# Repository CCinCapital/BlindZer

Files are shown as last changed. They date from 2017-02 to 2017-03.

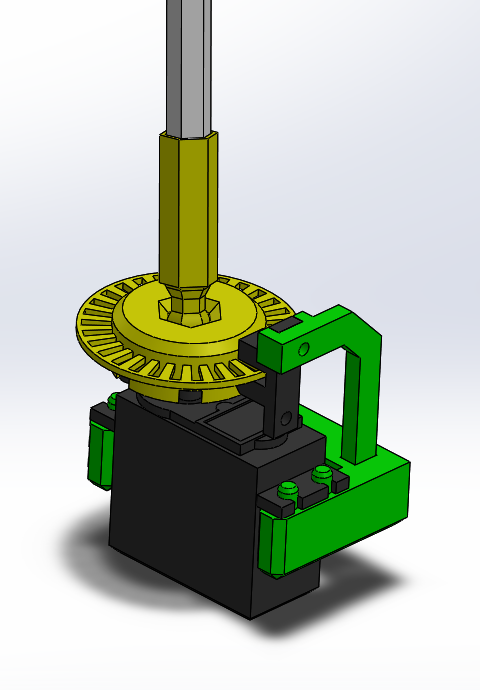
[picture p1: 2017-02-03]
Assembling Instruction/12. Fully Assembled (2).PNG

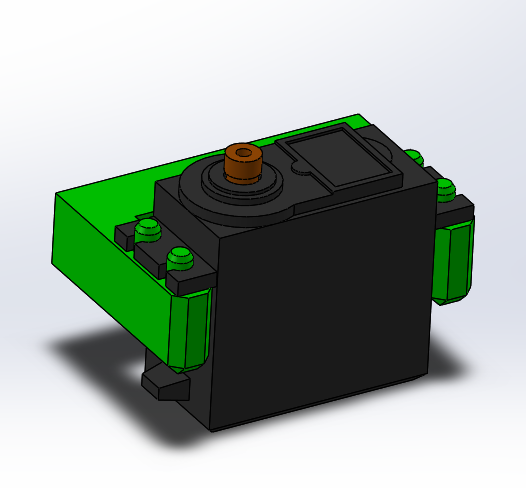
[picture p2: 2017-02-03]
Assembling Instruction/06. Servo Mount Assembly (2).PNG

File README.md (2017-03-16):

# BlindZer
Wireless enabled Window Blinds Roller<br>

<br>

### Video DEMO
[to be inserted HERE]
### Assembly Preview
<a href="https://github.com/CCinCapital/BlindZer/blob/master/3D%20STL%20Files/Assemly_PREVIEW.STL">Click Here</a>
### Compatibility
    + Window Blinds with hexagonal Rod. [Rod thickness: 8mm edge to edge]
### Software Requirement
    + Arduino IDE with ESP8266 Board Support package installed
    + Python
### Hardware Requirement
    + Access to 3D printer
    + Node MCU v0.9
    + TowerPro MG996R Servo Pack [Modified for continous rotation]
    + IRL2703 or any NMOS that able to drive Id > 500ma when Vgs = 3.3v
    + TCST2103 Optical Interrupter
    + Few Resistors [2K x1 ; 2.2K x2; 3.3K x1; ]
    + Breadboard or Protoboard
    + Jumper wires
    + Scerw [M3 x1 ; Wall Mounting x2 ]
    + Soldering Station & Solder & Flux
    + Phillip screwdriver 
    + Wire cutter & Pilers
### Installation
#### Hardware
       ----- Circuit -----
    1. Build the circuit by refering ../Schematic/BlindZer_Sche.pdf
    
       ----- Part Assembly -----
    1. Navigate to "../3D STL Files/" folder of this project
    2. 3D print all the .STL part at 1:1 ratio [mm]
    3. Assemble the 3D printed part refer to the instruction in "../Assembling Instruction/"
    
       ----- Modify the Servo -----
    1. Modify the servo for continous rotation [Follow the instruction below]
<a href="http://www.instructables.com/id/How-to-hack-a-servo-for-continuous-rotation-Towe/?ALLSTEPS">Click here to learn "How to modify a servo for continous rotation?"</a>
#### Software
    1. Clone or Download this repository
    2. Install the runtime environment
    
       ----- Modify Arduino Code -----
    3. Navigate to the Code at ../Code/Main/Main.ino
    4. Modify the code (Change the SSID and PASSWORD parameter) 
    5. Upload code to your board and observe the Serial Terminal to find line "Use this URL to connect: http://xxx.xxx.xxx.xxx"
    6. Record the URL
  
       ----- Modify Python Code -----
    7. Navigate to the Script at ../Code/GUIhttpRequest.py   
    8. Edit the Code and change the [self.IP = "xxx.xxx.xxx.xxx"] parameter to the IP recorded (URL without 'http://')

## Usage
       ----- Powering the BlindZer -----
    1. Use USB cable (directly plug into the onboard usb jack of NodeMCU)
    2. Powering using 4 x AA battery through the 2Pin header (see schematic)

       ----- Control using Webpage -----    
    1. Open the URL in a WebBrwoser
    
       ----- Control using Python GUI -----
    1. Run the GUIhttpRequest.py
## TODO
       ----- Firmware -----
    - Remember current position
    - implement Sleep(); and Weakup();
    
       ----- Python -----
    - Automatically control the BlindZer based on weather/time/Sun Height information
## Contributing
    + Fork it
## Credits
    http://www.instructables.com/id/Quick-Start-to-Nodemcu-ESP8266-on-Arduino-IDE/  by Magesh Jayakumar
## License
<br />This work is licensed under a <a rel="license" href="http://creativecommons.org/licenses/by-nc-sa/4.0/">Creative Commons Attribution-NonCommercial-ShareAlike 4.0 International License</a>.

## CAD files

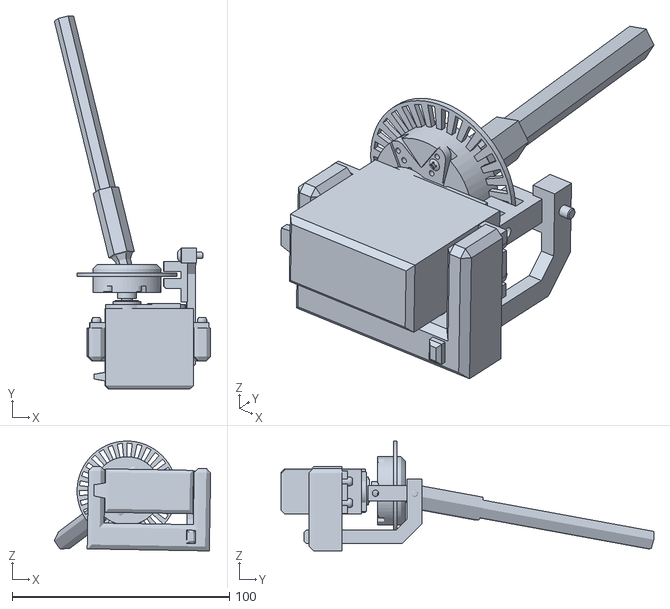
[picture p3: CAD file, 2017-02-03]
3D STL Files/Assemly_PREVIEW.STL
72.1 x 171.9 x 50.6

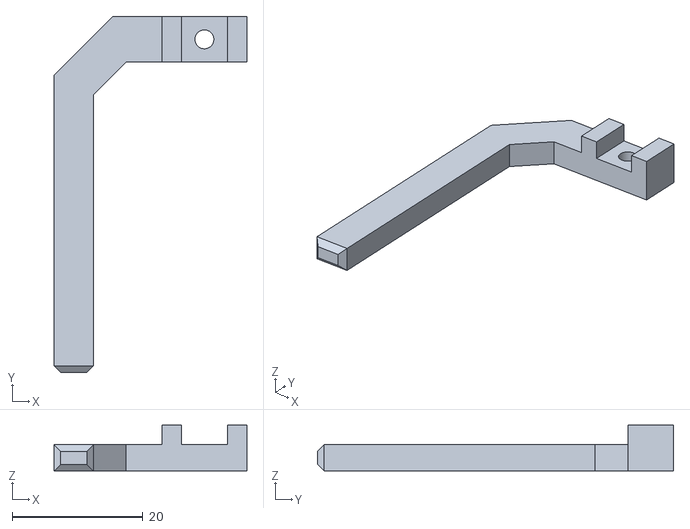
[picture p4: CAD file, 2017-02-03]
3D STL Files/InterrupterMount.STL
29.5 x 54.5 x 7.00

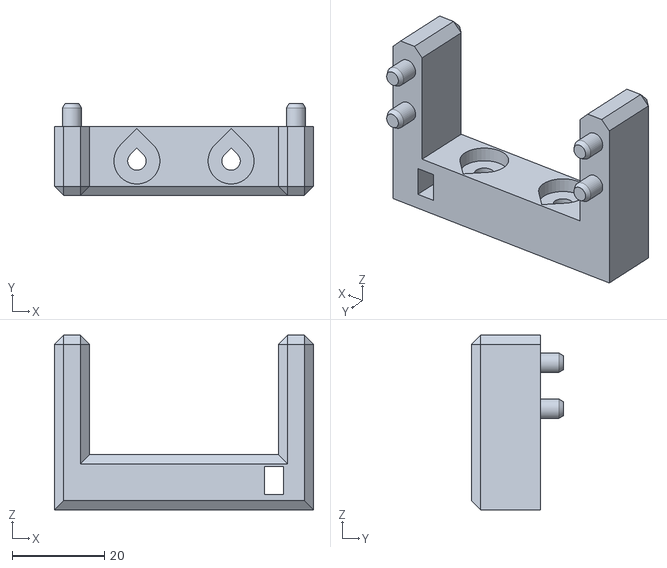
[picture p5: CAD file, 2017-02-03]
3D STL Files/ServoMount.STL
56.3 x 20.0 x 38.0

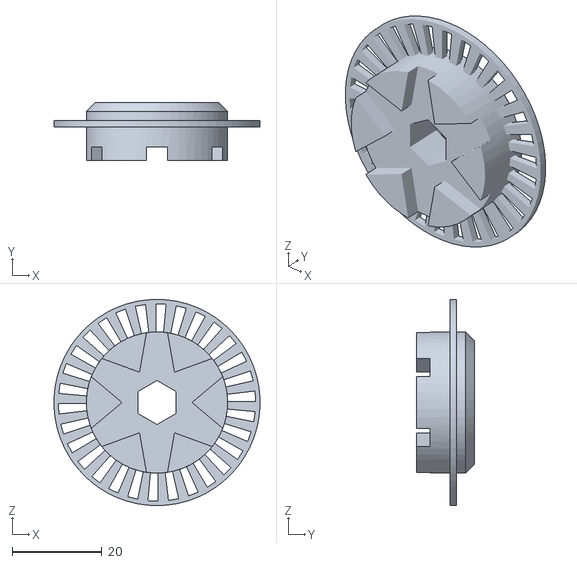
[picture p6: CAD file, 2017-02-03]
3D STL Files/ServolClampWithEncoder.STL
45.9 x 13.0 x 46.0

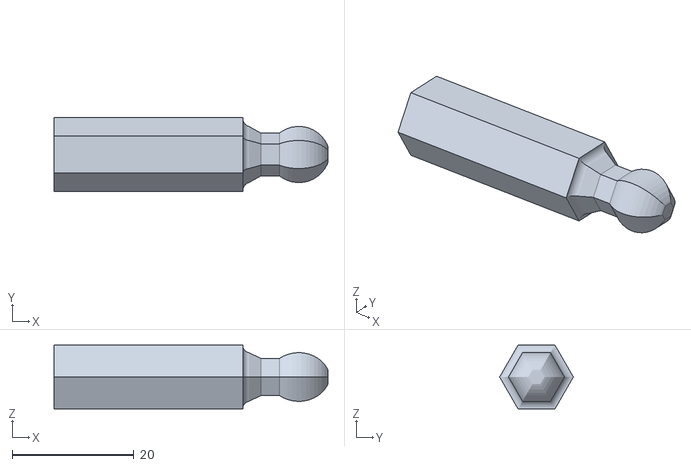
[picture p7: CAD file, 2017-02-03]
3D STL Files/BlindsRodAdapter.STL
45.0 x 12.1 x 10.5

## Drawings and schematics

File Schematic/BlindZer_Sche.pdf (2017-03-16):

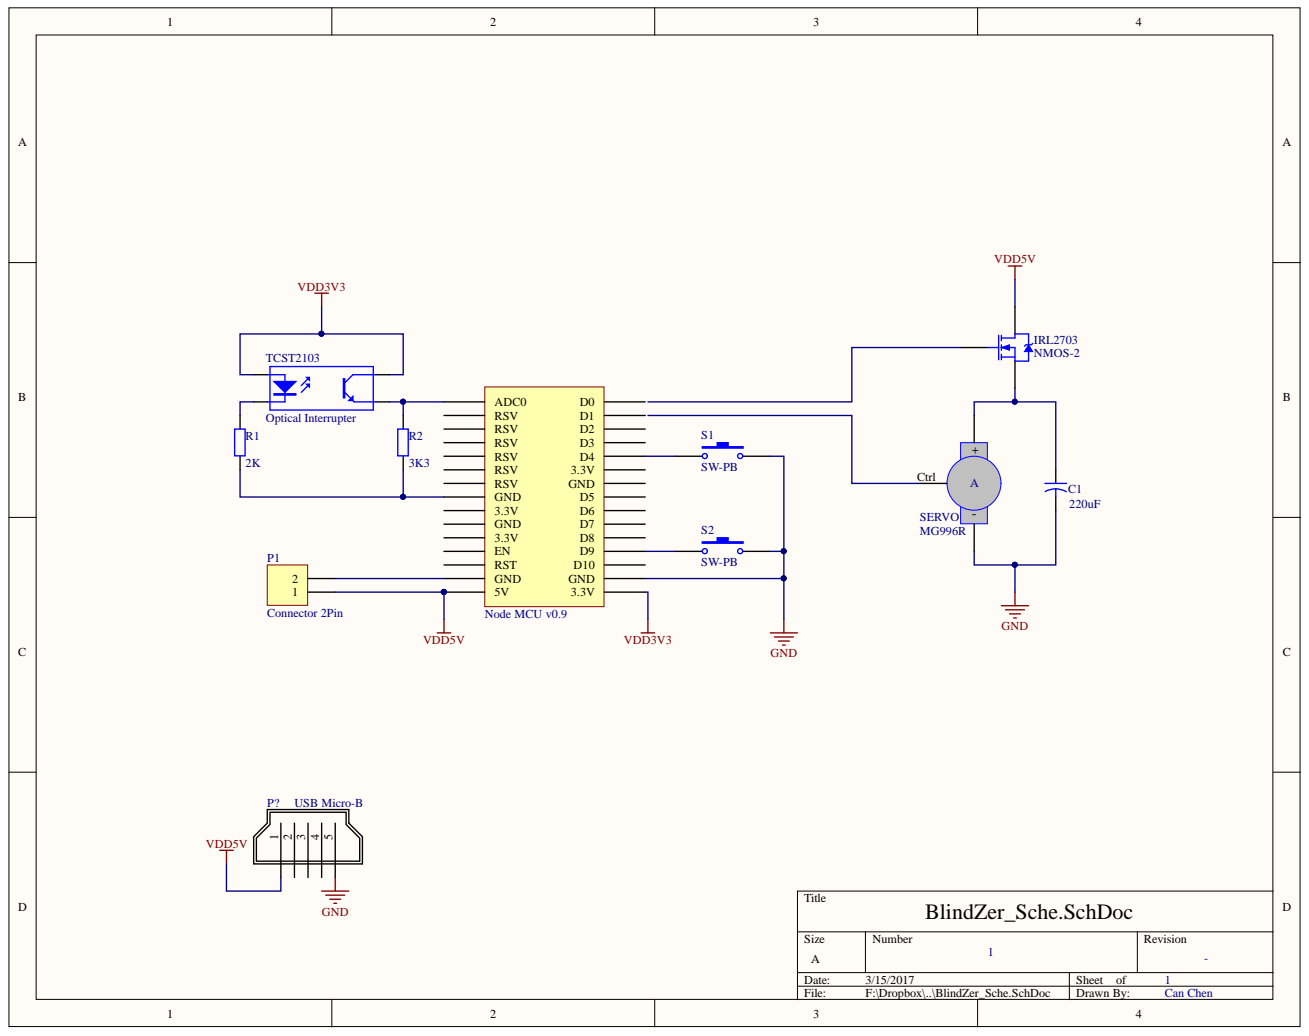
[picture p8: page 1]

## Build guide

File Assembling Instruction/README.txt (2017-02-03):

How to Assemble the Assembly?
- Follow pic 1 ~ 12

What else do I need to follow?
- Step 1~2: There is no predrilled hole for the screw, please force the screw into the Encoder whell
- Step 3~4: Screw size is M3, no screw nut is required to hold the interrupter securily
- Step 5~6: 
- Step 7~8: The feet of Optical Interrupter Assembly might require some trimming in order to fit into Servo Mount (Error introduced by FDM printer)
- Step 9~10: Please note the gap between blinds rod and the adapter, this is recommended for easier installation and operation

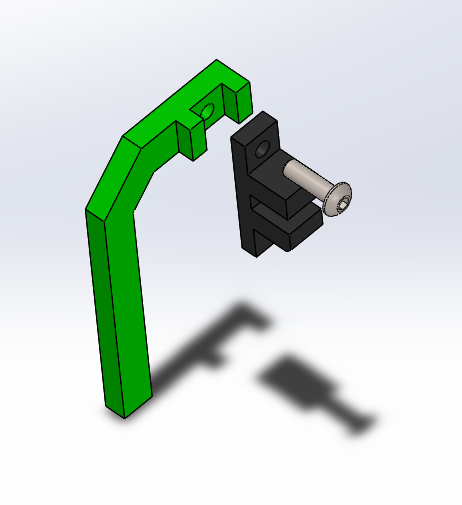
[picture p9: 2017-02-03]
Assembling Instruction/03. Optical Interrupter Assembly (1).PNG

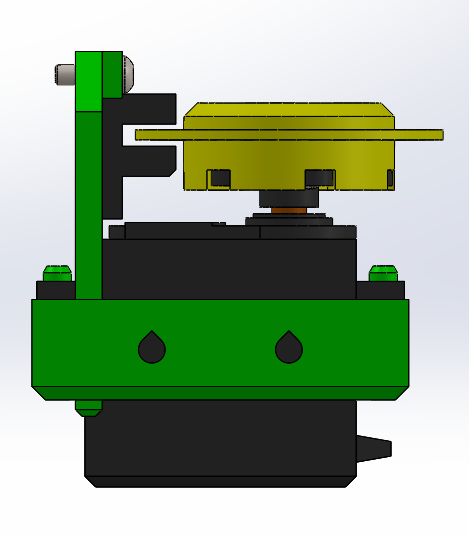
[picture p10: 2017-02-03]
Assembling Instruction/08. Full Assembly (2).PNG

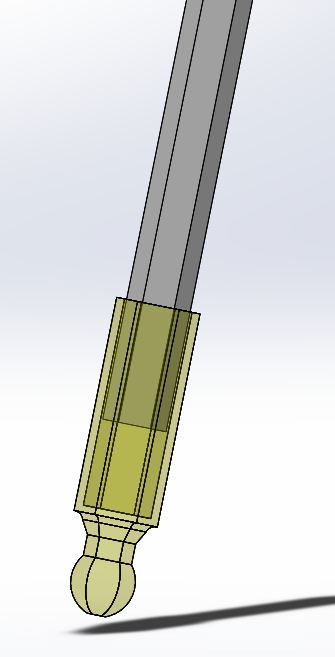
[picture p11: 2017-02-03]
Assembling Instruction/10. Hex Rod Adapter Assembly (2).PNG

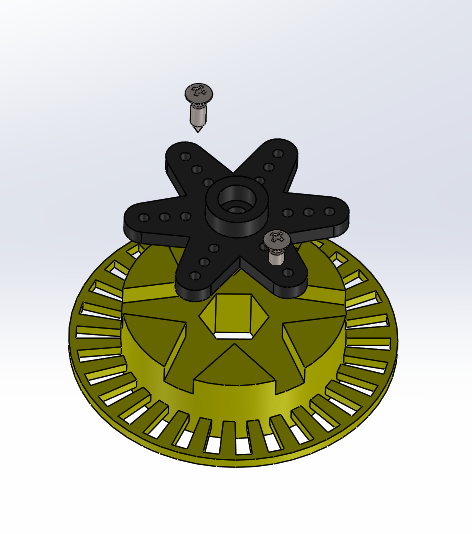
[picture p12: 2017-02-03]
Assembling Instruction/01. Encoder Whell Assembly (1).PNG

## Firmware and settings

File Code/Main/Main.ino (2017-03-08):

/*  
 *   ----------------------------About---------------------------- 
 *   This Program controls a wireless enabled device that rolls window blinds
 *   -- Author: Can Chen 
 *   -- More Details at: https://github.com/CCinCapital/Blinder/
 *   
 *   ----------------------------Brief----------------------------
 *   User may send commands remotely(HTTP request) to the servo to control its behavior  
 *   
 *   --------------------------Hareware---------------------------- 
 *   The device contains : 
 *    - one NodeMCU v0.9 (ESP8266-12) 
 *    - one TowerPro MG996R Servo
 *    - one NMOS
 *    - two Push Button
 *   ***************************Note*******************************
 *     Make sure to modify SSID(Line 54) and PASSWORD(Line 55) 
 *     to connect the device to your local WLAN
 */

// Preprocessors
#include <ESP8266WiFi.h>
#include <Servo.h>

// Pin defination
#define D1 5
#define D2 4
#define D3 0
#define D4 2
#define D5 14
#define D6 12
#define D7 13
#define D8 15
#define D9 3
#define D10 1

// optical Interrrupter Trigger threshold
#define IR_Through 700
#define IR_Blocked 300

// servo rotation direction and default steps
/* 
 *  Note: Servo was modified to think it's always at the middle (92) position
 *        so, number greater than 92 will cause it to rotate clockwise
 *        and number smaller than 92 will cause it to rotate counter clockwise
 *        by writing 92 to the servo will cause it to stop (idealy)
 *        -- the difference between numbers determines the rotation speed
*/       
#define Servo_Clockwise 70
#define Servo_Counter_Clockwise 110
#define Servo_Half_Cycle 30    // One full rotation of the servo (determined by the Optical Encoder Whell's resulotion)

// SSID and Password used to connect to Router
const char* ssid = "YourWiFiNameHere";
const char* password = "YourWiFiPasswordHere";

// Create WiFi Server and Servo
WiFiServer server(80);
Servo myServo;

// Run Once
void setup() {
  // Set the baud rate for Serial communication between Board and PC
  Serial.begin(115200);
  delay(10);
  
  // Port Directions
  pinMode(D1, OUTPUT);              // NMOS
  pinMode(D2, OUTPUT);              // Servo
  
  pinMode(A0, INPUT);               // Optical Interrupter
  pinMode(D4, INPUT_PULLUP);        // Push button 1 (Pull-Down)
  pinMode(D9, INPUT_PULLUP);        // Push button 2 (Pull-Down)

  // Attach servo to pin D2
  myServo.attach(D2);

  // Set interrupt listener
  // ([Pin to listen], [Function to run upon event], [Event to listen])
  attachInterrupt(digitalPinToInterrupt(D4),ISR_1, FALLING);
  attachInterrupt(digitalPinToInterrupt(D9),ISR_2, FALLING);

  // Connecting to Router & Print out the status though Serial terminal
  Serial.println();
  Serial.println("Connecting to ");
  Serial.println(ssid);
  WiFi.begin(ssid, password);
  while (WiFi.status() != WL_CONNECTED) {
    delay(500);
    Serial.print(".");
  }
  Serial.println();
  Serial.println("WiFi Connected.");
  
  server.begin();
  Serial.println("Server started.");
  
  // Start up test
  Serial.println("Start Servo Test");
  digitalWrite(D1, HIGH);
  delay(15);
  blindsControl(Servo_Clockwise,Servo_Half_Cycle);
  delay(15);
  digitalWrite(D1, LOW);
  delay(15);
  digitalWrite(D1, HIGH);
  delay(15);
  blindsControl(Servo_Counter_Clockwise,Servo_Half_Cycle);
  delay(15);
  digitalWrite(D1, LOW);
  Serial.println("Servo Test Finished");

  Serial.print("Use this URL to connect: ");
  Serial.print("http://");
  Serial.print(WiFi.localIP());
  Serial.println("/");
}

void loop() {
  // Check if a client has connected
  WiFiClient client = server.available();
  if (!client) {
    return;
  }
  
  // Wait until the client sends some data
  Serial.println("new client");
  while(!client.available()){
    delay(1);
  }
  
  // Read the first line of the client's request
  String request = client.readStringUntil('\r');
  Serial.println(request);
  client.flush();
    
  // Match the request
  if (request.indexOf("/Servo=UP") != -1)  {
    blindsControl(Servo_Clockwise,Servo_Half_Cycle);
  }
  if (request.indexOf("/Servo=DOWN") != -1)  {
    blindsControl(Servo_Counter_Clockwise,Servo_Half_Cycle);
  }

  // Send the HTTP webpage to client
  client.println("HTTP/1.1 200 OK");
  client.println("Content-Type: text/html");
  client.println(""); //  do not forget this one
  client.println("<!DOCTYPE HTML>");
  client.println("<html>");
  client.print("Please choose the operation of Servo:");
  client.println("<br><br>");
  client.println("<a href=\"/Servo=UP\"\"><button>Roll UP </button></a>");
  client.println("<a href=\"/Servo=DOWN\"\"><button>Roll DOWN </button></a>");
  client.println("</html>");
 
  delay(1);
  Serial.println("Client disonnected");
  Serial.println("");
}

/*  --Method that controls the motion of Servo--
 *  INPUT:  roller direction
 *          steps to rotate
 *  OUTPUT: Debugging information through serial
 *  RETURN: None
 */
void blindsControl(int Roller_Direction, int Steps) {
  // Declare local variables
  int IR_Reading = analogRead(A0);    
  int Previous_Servo_Staus = IR_Reading;            // 1 => IR signal blocked (Optical Interrupter)
  int Current_Servo_Staus = Previous_Servo_Staus;   // 2 => IR signal through (Optical Interrupter)
  
  digitalWrite(D1, HIGH);                 // Power Up Servo (Close the NMOS switch)
  delay(5);                              // Wait Servo to Boot Up
  myServo.write(Roller_Direction);        // Give Servo direction to rotate
  
  int Steps_Count = 0;
  while(Steps_Count < Steps){
    //Serial.println("Rotating ");
    //Serial.print(Steps_Count);
    
    // Read status of Optical Interrupter 
    IR_Reading = analogRead(A0);   
    // Compare the reading to Triggering Threshold
    // Store the current servo status if conditions are met       
    if (IR_Reading >= IR_Through) {
      Current_Servo_Staus = IR_Through;
    }
    else if (IR_Reading <= IR_Blocked) {
      Current_Servo_Staus = IR_Blocked;
    }

    // Compare the previous servo staus and its current status
    // if difference were found, record new status, increment step count
    if (Previous_Servo_Staus != Current_Servo_Staus) {
      Previous_Servo_Staus = Current_Servo_Staus;
      Steps_Count += 1;
    }
  }
  myServo.write(92);
  delay(5);
  digitalWrite(D1, LOW);                  // Power Down Servo (Open the NMOS switch)
  //Serial.println("servo stopped");
}

/* --Interrupt Service Routine ONE--
 * --Turn Servo Clockwise about # of Steps(Default)--
 * INPUT: NONE 
 * OUTPUT: NONE
 * RETURN: NONE
 */
void ISR_1() {
  blindsControl(Servo_Clockwise,Servo_Half_Cycle);
}

/* --Interrupt Service Routine TWO--
 * --Turn Servo Counter Clockwise about # of Steps(Default)--
 * INPUT: NONE 
 * OUTPUT: NONE
 * RETURN: NONE
 */
void ISR_2() {
  blindsControl(Servo_Counter_Clockwise,Servo_Half_Cycle);
}

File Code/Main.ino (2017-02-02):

#include <Servo.h>
#define D1 5
#define D2 4
#define D5 14
#define D6 12

#define High 700
#define Low 300

Servo myServo;
int reading = 0;
int step_count = 0;

void setup() {
  Serial.begin(115200);
  // put your setup code here, to run once:
  pinMode(D1, OUTPUT);
  pinMode(D2, OUTPUT);
  
  pinMode(A0, INPUT);
  pinMode(D5, INPUT);
  pinMode(D6, INPUT);

  myServo.attach(D2);

  attachInterrupt(digitalPinToInterrupt(D5),ISR_1, HIGH);
  attachInterrupt(digitalPinToInterrupt(D6),ISR_2, HIGH);
  
  digitalWrite(D1, HIGH);
  delay(15);
  blindsControl(110,59);
  delay(15);
  blindsControl(92,1);
  delay(15);
  digitalWrite(D1, LOW);
  delay(15);
  digitalWrite(D1, HIGH);
  delay(15);
  blindsControl(70,59);
  delay(15);
  digitalWrite(D1, LOW);
}

void loop() {
  yield();
}

void blindsControl(int roller_direction, int steps) {
  //Serial.println("defining parameters");
  boolean previous_position = false;
  boolean current_position = false;
  int interrupter_reading = analogRead(A0);
  int step_count = 0;
  //Serial.println("entering loop");
  while(step_count < steps){
    if (interrupter_reading >= High) {
      current_position = true;
    }
    else if (interrupter_reading <= Low) {
      current_position = false;
    }
    if (previous_position != current_position) {
      previous_position = current_position;
      step_count += 1;
    }
    //Serial.println("in loop");
    digitalWrite(D1, HIGH);
    delay(15);
    myServo.write(roller_direction);
    interrupter_reading = analogRead(A0);
  }
  //Serial.println("stopping servo");
  myServo.write(92);
  delay(15);
  digitalWrite(D1, LOW);
  //Serial.println("servo stopped");
}

void ISR_1() {
  Serial.println("D5 Interrupted");
  blindsControl(110,59);
}

void ISR_2() {
  Serial.println("D6 Interrupted");
  blindsControl(70,59);
}

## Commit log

2017-01-25 Initial Commit
    Submityed all STL files
    [Assem1.SLDASM, BasePlate.SLDPRT, BlindRodAdapter.SLDPRT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]
2017-02-02 Move Files
    move files into more organized directory
    [Assem1.SLDASM, BasePlate.SLDPRT, BlindRodAdapter.SLDPRT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]
2017-02-02 Change pushbutton to 'pull down'
    also added more pin defination
2017-02-02 Change Interrupt triggering method
    Also changed the wifi server page
2017-02-02 FIxed A Crash by reducing loop length
    loop too long caused watchdog timer to trigger reset
    [Main.ino]
2017-02-02 Add Feature
    A simple python GUI to controll the Servo
2017-02-02 Modified .gitignore to exclude few files
    [Assem1.SLDASM, BasePlate.SLDPRT, BlindRodAdapter.SLDPRT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]
2017-02-02 Hide More SLD Files
    [Assem1.SLDASM, ChasisBaseSLDPRT.SLDPRT, EncoderWheel.SLDPRT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]
2017-02-02 Show Some STL Files
    [BlindRodAdapter.STL, BlindRodAdapterB.STL, InterrupterMount.STL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]
2017-02-03 Upload Schematic
    [BlindZer_Sche.SchDoc]
2017-02-03 Upload Assembling Instructions and Newest Version of .STL files
    [BlindRodAdapter.STL, BlindRodAdapterB.STL, BlindZer_Sche.SchDoc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]
2017-02-03 Upload the fully assembled BlindZer for preview
    [Assemly_PREVIEW.STL]
2017-03-16 Update Schematic
    [BlindZer_Sche.SchDoc]
